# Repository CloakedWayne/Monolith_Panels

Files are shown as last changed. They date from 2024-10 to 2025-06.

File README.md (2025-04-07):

[][cc-by-nc-sa]

# Monolith Panels for Voron 2.4 and Trident

### 1515 extrusion version by CabbageCorp can be found [here](https://github.com/CloakedWayne/Monolith_Panels/tree/main/Usermods/CabbageCorp/Mini_Monolith).

<br/>



Join the Discord (https://discord.gg/JanBKxAzDz)

## What's this?
Overcomplicated panels.



## Use:
- The CAD contains everything that's needed for V2/VT 250/300/350mm with BOM thickness panels (3mm) and is also **a good assembly guide**.

- The vertical printed part length is determined by the theoretical Z travel and NOT the bed size. Pick the vertical part length based on the Z travel of your machine. Tridents usually have a 250mm Z regardless of the bed size, except the cubed kits.

- It's intended to be used with **another layer of 3mm foam tape** or with 5mm foam tape paired with 4mm panels (Monolith Gantry stepper protrusion is 3.6mm).

- Feel free to remix the parts for different setups!

- Parts will load in the correct orientation when exported.

- The corners can be used without the straights, but your mileage may vary if you don't put VHB on them.

- When used as a panel frame you can get away with putting VHB only in the middle.

- Recommended **shrinkage compensation** for the parts when printed in **ABS is 99.3-99.5%**. Make sure to test this before committing to printing huge amounts of plastic, because shrinkage can be 3-4mm in total.

- Clips are fairly sensitive to EM/PA, but can be easily scaled to fit perfectly in the other plastic parts. They're not sensitive to alu extrusion tolerances.



## BOM
### DISCLAIMER: This is a challenging mod and a lot of the stuff is still untested. The BOM quantities can greatly vary based on how you build it. Always refer to CAD.



|No.|Description|Qty|
|---|---|---|
|1.|M3x16 SHCS or BHCS|probably more than 10|
|2.|M3x6 BHCS or M3x8 FHCS (better)|definitely more than 10|
|3.|M3 nuts|probably more than 10|
|4.|M3x5x4mm heatset inserts|definitely more than 10|
|5.|VHB tape|enough|
|6.|Foam tape|enough|
|7.|4mm OD PTFE tube|exactly 96mm|



If you've any got questions you can find me on Discord ***@CloakedWayne***
<br/><br/><br/><br/>
This work is licensed under a
[Creative Commons Attribution-NonCommercial-ShareAlike 4.0 International License][cc-by-nc-sa].

[][cc-by-nc-sa]

[cc-by-nc-sa]: http://creativecommons.org/licenses/by-nc-sa/4.0/
[cc-by-nc-sa-image]: https://licensebuttons.net/l/by-nc-sa/4.0/88x31.png
[cc-by-nc-sa-shield]: https://img.shields.io/badge/License-CC%20BY--NC--SA%204.0-lightgrey.svg

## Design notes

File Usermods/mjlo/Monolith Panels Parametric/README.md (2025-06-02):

# Parametric Monolith Panels

I like Monolith Panels, but I wanted thicker panels to trap more heat. Design is not exactly the same as Wayne's original, more "inspired by".
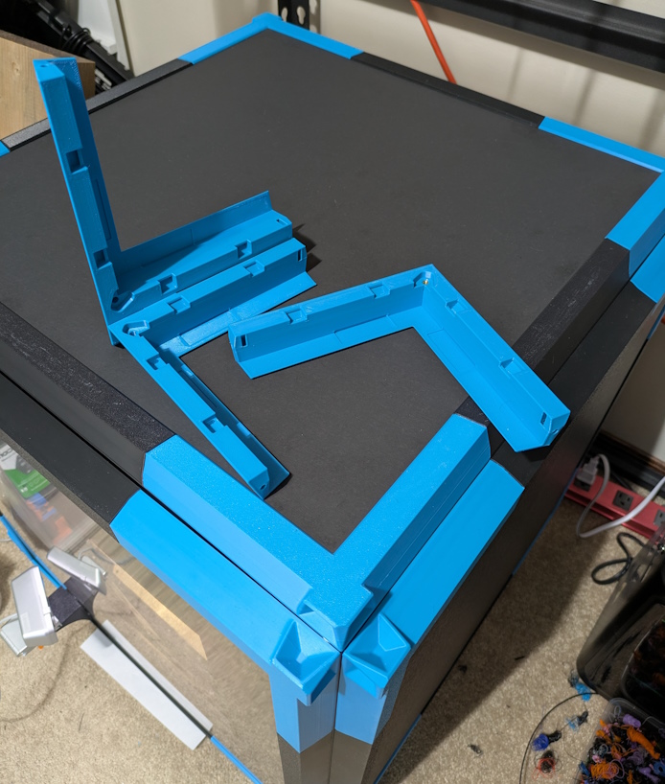
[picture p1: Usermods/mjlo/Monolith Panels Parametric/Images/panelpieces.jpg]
Thicker Monolith Panel pieces


# How to use
Upload the CAD file to fusion, open it, click "Modify" > "Change Parameters". Most parameters have a description or are self explanatory, but I am not good with words so YMMV.

Printing, BOM, and assembly should be pretty much the same as the originals, aside from the change in panel material.

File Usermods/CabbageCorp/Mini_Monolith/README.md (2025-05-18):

# Mini Monolith

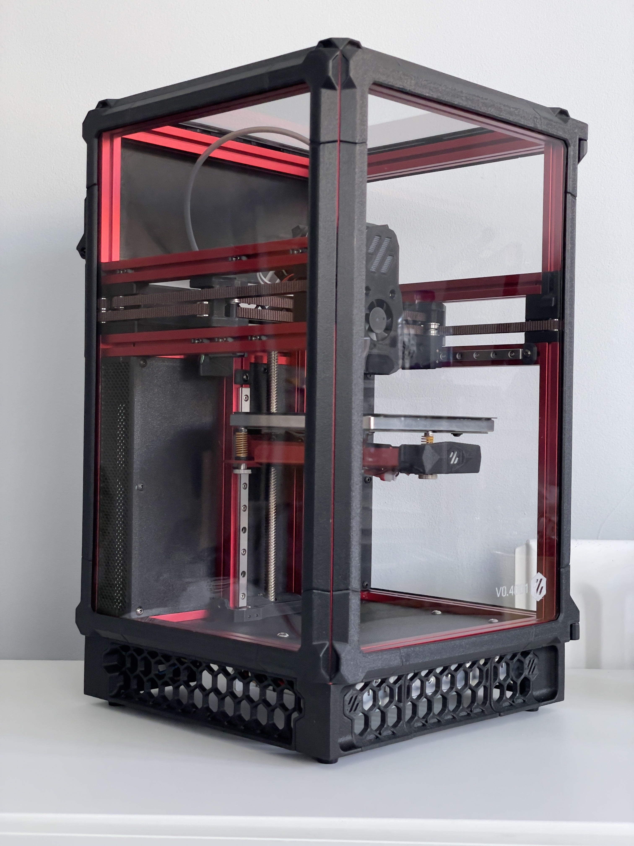
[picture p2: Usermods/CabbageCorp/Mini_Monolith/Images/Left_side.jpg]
Left_side


## Intro

Mini Monolith is an adaptation of monolith panels from CloakedWayne with zeropanel clips from zruncho, adapted for 1515 extrusions and PFA’s.

I’ve seen a couple of really nice mini-monolith versions floating around, and have been waiting for release but needed something for my build so threw this together quickly.

This is currently only sized for 100mm tophat V0.2’s and any PFA variants like the Hex-Zero that has a 348mm vertical height. However, geometry is fairly easy to modify so cutting and extruding would allow different lengths for other PFA’s (please upload and share).

Unfortunately, I forgot that monolith doesn’t have a door closure system for a trident or V0 type hinged door so I’ve just been using 3 clips to keep the door closed. ColonyClacker/Mini Fridge Door can be added with the additional verticals, hardware can be found (soon) on the [ColonyClacker](https://github.com/PrintersForAnts/ColonyClacker) repo. [If you like this project and want to help me get free filament, feel free to drop a like and download cad/stl’s from makerworld here](https://makerworld.com/en/models/1300382-mini-monolith-panels-for-voron-v0-v0-2-1515-pfa#profileId-1332588)

## Why Mini Monolith?

- Full panels sized panels help eliminate leakage through tophat panel gaps
- Compatibility with relaxed fit mini-fridge door panels (329mm x 209mm) for easy sourcing
- Similar panel stack to zero panels (6.8mm total squish height of 1mm VHB + 3mm panel +3mm foam)
- Mini monolith allows 2.8-3mm spacing between the frame and panels -allowing Pandora’s box and Hex-zero variants to have extra space for gantry
- Strong clamping force to enable thicker foam and more squish
- Extrusions covered to minimise heat loss
- Recessed VHB tape slots for 4mm panels + 3mm foam (if you have 3mm panels+3mm foam, attach the VHB to the non-recessed parts of the frame for adequate squish)

### Main changes:

- Heatset inserts instead of trapped nuts to connect sections
- Through bolted heatset screw reinforcement
- Hinges adapted for m3x20 pins commonly found in extruders or PTFE tubes like the original monolith
- Various dimensional changes

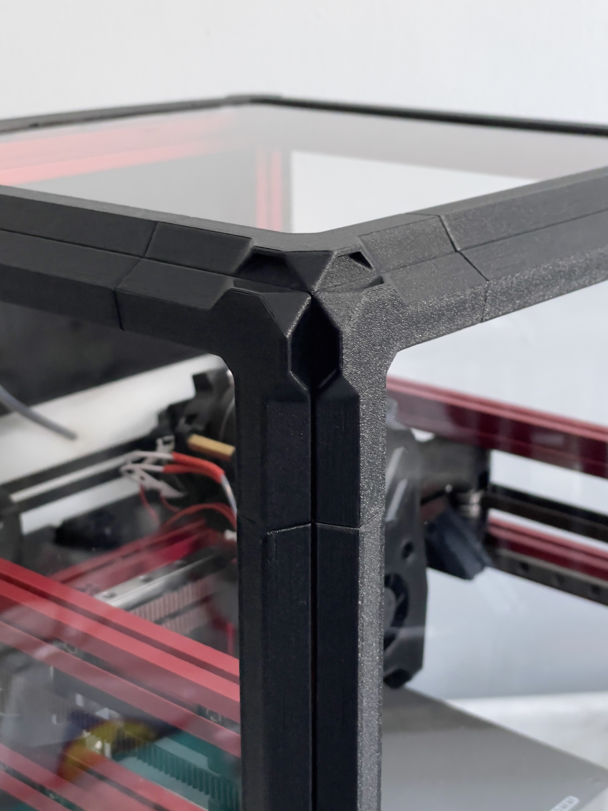
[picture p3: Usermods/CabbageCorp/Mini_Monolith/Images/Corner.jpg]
Corner

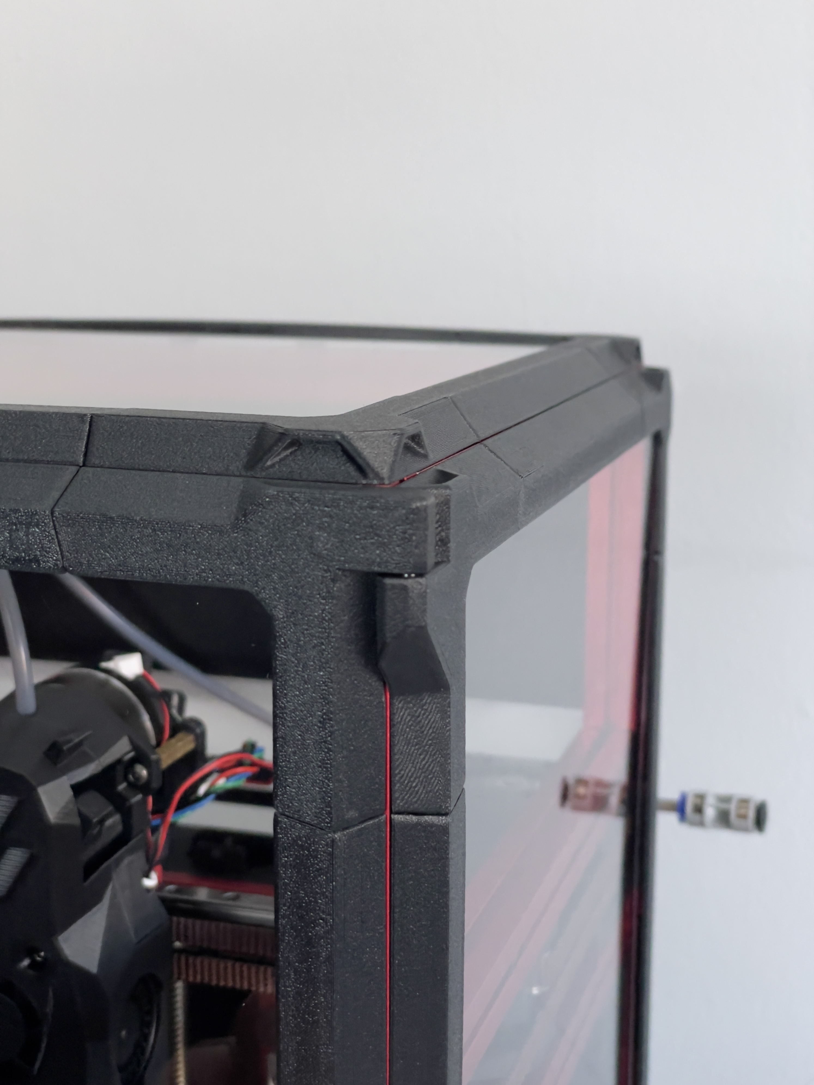
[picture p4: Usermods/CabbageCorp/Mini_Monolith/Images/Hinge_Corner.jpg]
Hinge_Corner

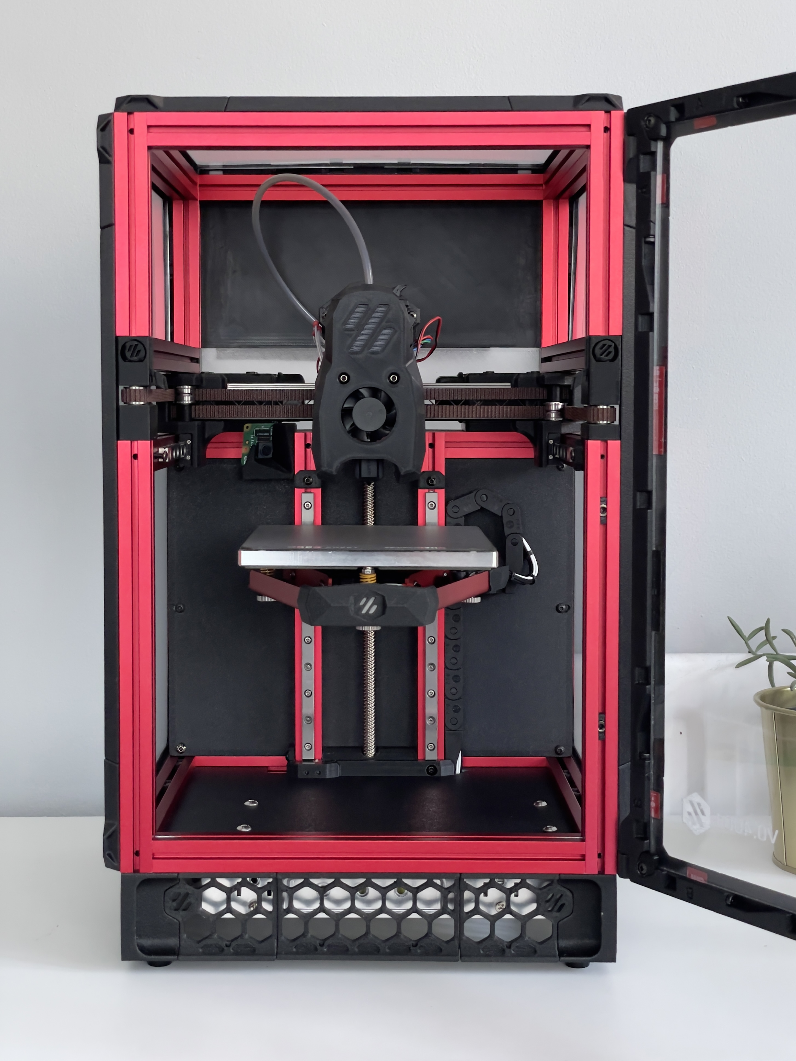
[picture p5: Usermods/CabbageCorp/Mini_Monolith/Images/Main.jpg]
Main

right_side

## BOM

- **Per side/panel**

    | Amount | Part | Notes  |
    | --- | --- | --- |
    | 12 | heatset inserts m3x5x4 (voron) | 3 per corner |
    | 8 | M3 x 16 BHSC/SHSC screws  | (10-16mm works) |
    | 1 roll | 1mm x 5mm VHB foam tape | Voron BOM VHB tape cut in half works |
    | 1 roll | 5-6mm wide, 3-5mm thick foam tape | 4.5m total for 3 panels + Top |
- **Hinges**

    | Part | Notes |
    | --- | --- |
    | 3x20mm pins | Common extruder pins |
    | 18mm PTFE tubes | 4mm OD |
- **Panels**
    
    1-3x Mini Fridge Door panels (relaxed fit 329mm x 209mm)
    
    1x 209x209mm top panel (nominal length of 210.8mm or 212x212mm using the experimental horizontals)
    
    | Qty. | Part | Notes |
    | --- | --- | --- |
    | 3 | Mini Fridge Door panels (3mm thick relaxed fit 329mm x 209mm) | Max dimensions: 329 x 210.8 |
    | 1 | 209x209mm top panel (3mm thick) | Max dimensions: 210.8 x 210.8 |
    | 0 | Experimental 212x212mm top panel (3mm thick) | Due to widening straights, the clips may be pushed towards the centreline and fall out of the printed frame easier |
- **Full coverage (2 Sides, Door and Top)**

    | Amount | Part | Notes  |
    | --- | --- | --- |
    | 48 | heatset inserts m3x5x4 (voron) | 3 per corner |
    | 32 | M3 x 16 BHSC/SHSC screws  | (10-16mm works) |
    | 1 roll | 1mm x 5mm VHB foam tape | Voron BOM VHB tape cut in half works |
    | 4.5M | 5-6mm wide, 3-5mm thick foam tape | 4.5m total for 3 panels + Top |
    | 2x | 3x20mm pins or 18mm PTFE tubes | 2 pins or 32mm ptfe total |
    | 3 | Mini Fridge Door panels (3mm thick relaxed fit 329mm x 209mm) | Max dimensions: 329 x 210.8 |
    | 1 | 209x209mm top panel (3mm thick) | Max dimensions: 210.8 x 210.8 |

## **Print notes:**

Like monolith, this is scaling/shrinkage sensitive with no compensation built in so tuned print profiles are strongly recommended. 

- Thin areas around screw access cutouts and corners are PA sensitive.
- Optional mouse ears on the longer sections are recommended for those that typically struggle with adhesion.
- If second layer perimeters are separating, turning off elephants foot compensation and dialing in first layers may help.
- The clips are the most sensitive part so make sure EM is perfect -if they are too loose, scaling them up slightly by 0.5-1% will help with hold.
- The model works best with 0.1mm increments but will still work fine at 0.2mm layer heights with no differences in testing. Initial layer height of 0.1 should work as well but is currently untested.
- Each panel will need 4 corners, either universal or hinged with 2 horizontals and 2 vertical straights. For 3 sided monolith and a tophat, you’d need to print:
    - 12x universal corners
    - 4x hinges
    - 6x vertical sections
    - 10x horizontal sections

*note: There is an experimental topside horizontal for stock 212x212mm panel size however, the extra width tilts the clips towards the centre. Frequent removal will likely result in loosening and clips being pulled out of the panels due to angle. Larger clip recommended.*

## **Assembly notes:**

Use the heatset tool to prevent bulging on the thin walls 




Ensure heatsets are fully inserted flush with the lowest edge

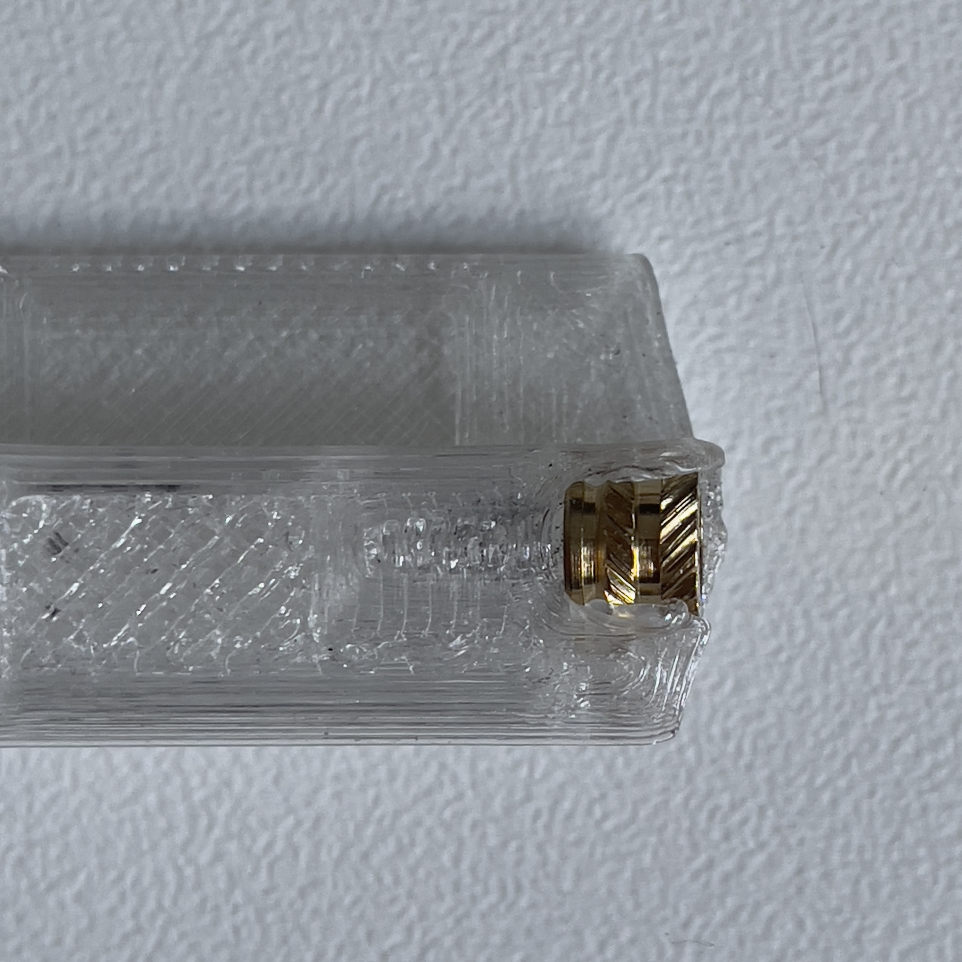
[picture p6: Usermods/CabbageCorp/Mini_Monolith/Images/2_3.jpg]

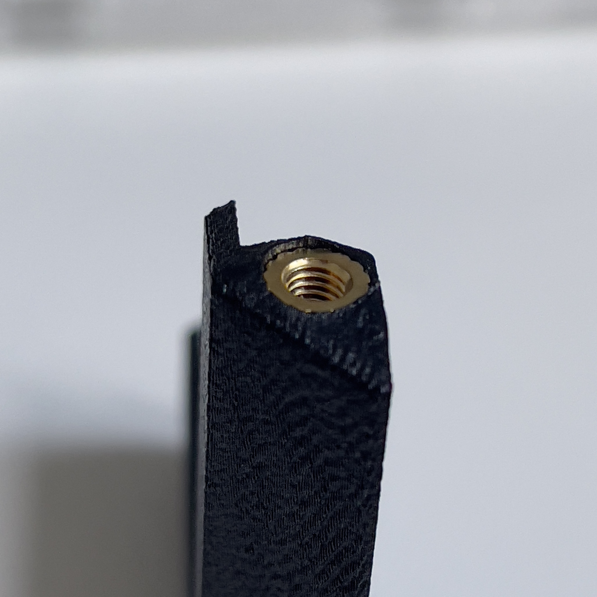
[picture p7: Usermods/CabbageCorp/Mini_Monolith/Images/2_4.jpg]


Press clips in firmly with something firm

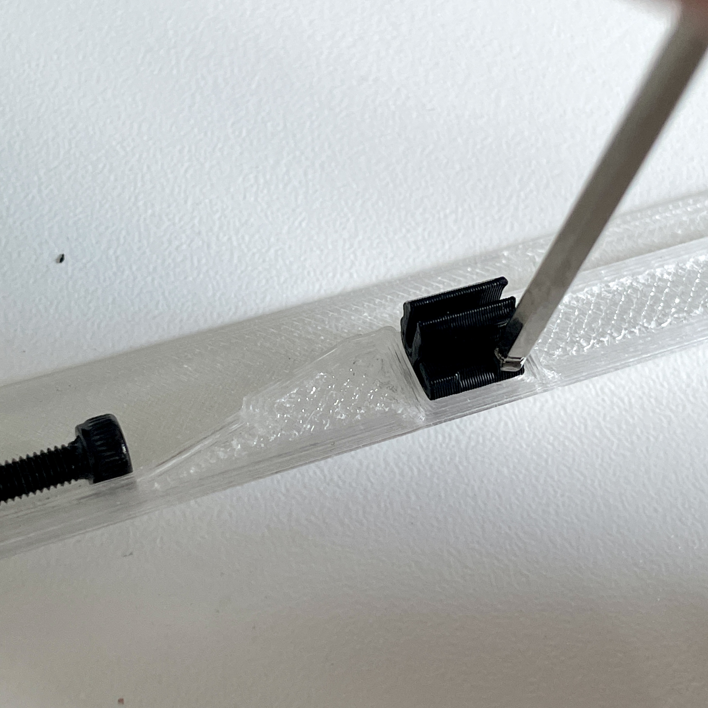
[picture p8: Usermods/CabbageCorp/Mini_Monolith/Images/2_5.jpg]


Corner panel clips: ensure the screws are fully tight and lower than flush with the frame.

Optional:

If using screws longer than 10mm, prethread the plastic by screwing it into corner before attaching the straight. To prevent heatset pull out, maintain pressure while tapping the plastic past the insert. 16mm M3 screws will add a bit of rigidity and help with heatset pull out.

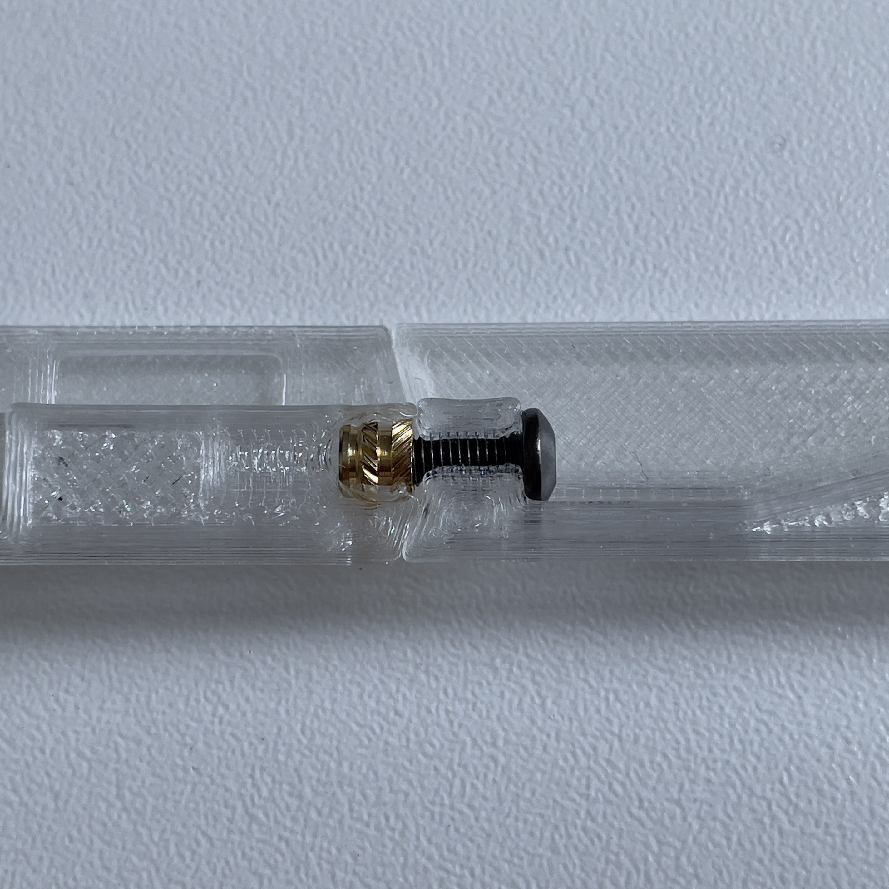
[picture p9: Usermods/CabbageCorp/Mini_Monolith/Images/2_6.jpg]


10mm minimum length

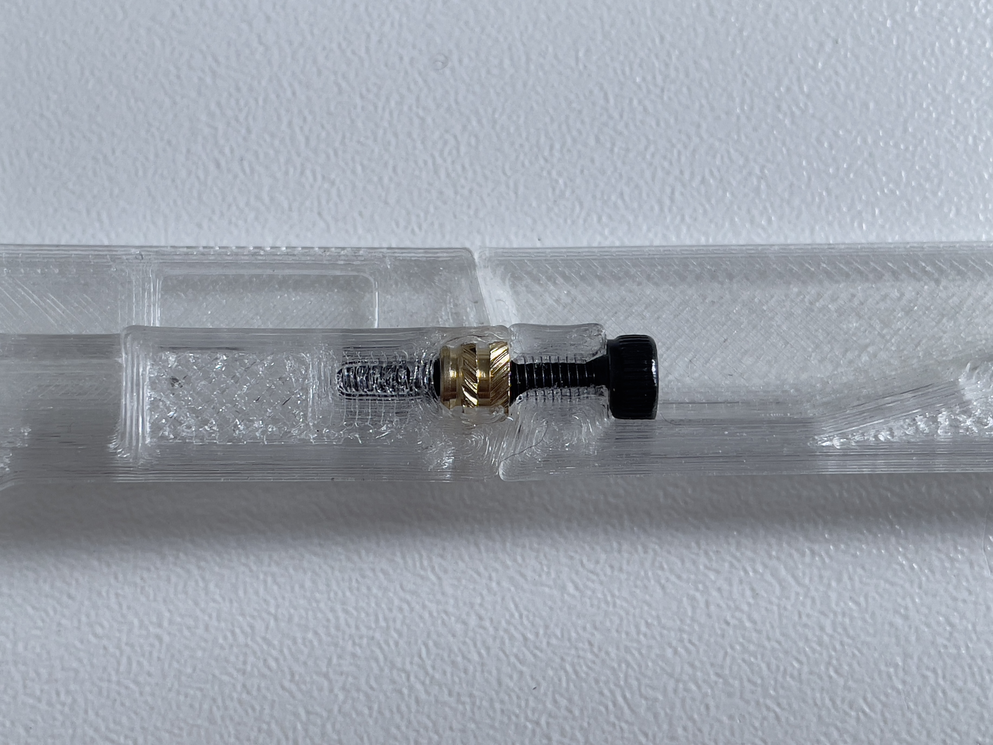
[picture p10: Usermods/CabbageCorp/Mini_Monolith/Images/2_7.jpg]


16mm Maximum length 

I’d like to give a big thanks to these people for their contribution that made this possible:

- CloakedWayne for his monolith design, concept, and amazingly neat/organised and easy to edit cad
- zruncho for his zeropanel clip geometry and research on panel stack
- #sonny5578, #chefha, and #brexited on Voron discord for teaching me cad and inputs
- Ukutghost #hamido. #simonsaysty - special thanks to you guys for wasting filament, beta testing tolerances, finding print issues and giving suggestions.
- #tigsteruk and Ukutghost- for being enthusiastic and helping me feel like my cad isn’t too janky to be shared
- #seti118- for getting panels to me so fast

License note:

Zruncho's ZeroPanels clip geometry retains its original licence that can be found [here](https://github.com/zruncho3d/ZeroPanels?tab=GPL-3.0-1-ov-file#readme).

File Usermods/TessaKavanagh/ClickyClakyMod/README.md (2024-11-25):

# TessaKavanagh ClickyClakyMod
##Acknowledgments:
Special thanks for additions, goes to: 
@luxflow (optional 5mm parts and documentation)

## Spacer

- If you want to use the original clickyclaky parts, print spacers from [STLs/Monolith_Panels_ClickyClackyMod v2.3mf](STLs/Monolith_Panels_ClickyClackyMod%20v2.3mf)
  - There are two types of spacers (see below) 
  - The left one is for handle hinges (print twice), and the right one is for handle latch (print once).
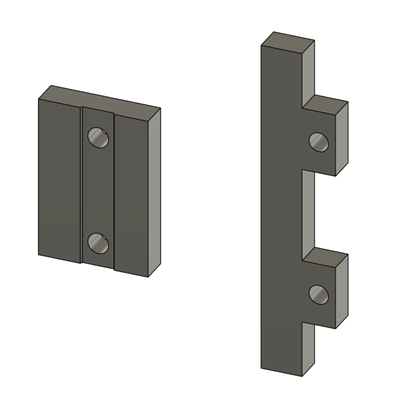
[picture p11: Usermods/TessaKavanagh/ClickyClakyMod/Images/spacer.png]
spacer

- If you don't want to use spacers, reprint the modded clickyclaky parts in [STLs/optional](STLs/optional/)

## Assembly

- To insert the door hinge side (mostly left side) monolith panels, you must detach door first.

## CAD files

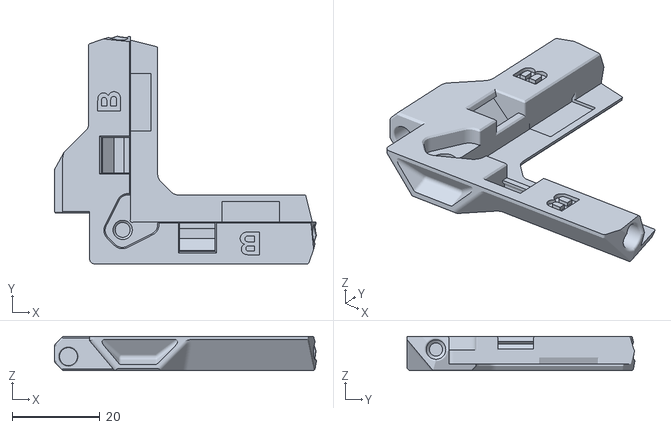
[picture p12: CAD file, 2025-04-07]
Usermods/CabbageCorp/Mini_Monolith/STLs/18mm PTFE Hinge/18mm Ptfe [a]_hinge_b.stl
59.8 x 52.0 x 7.80

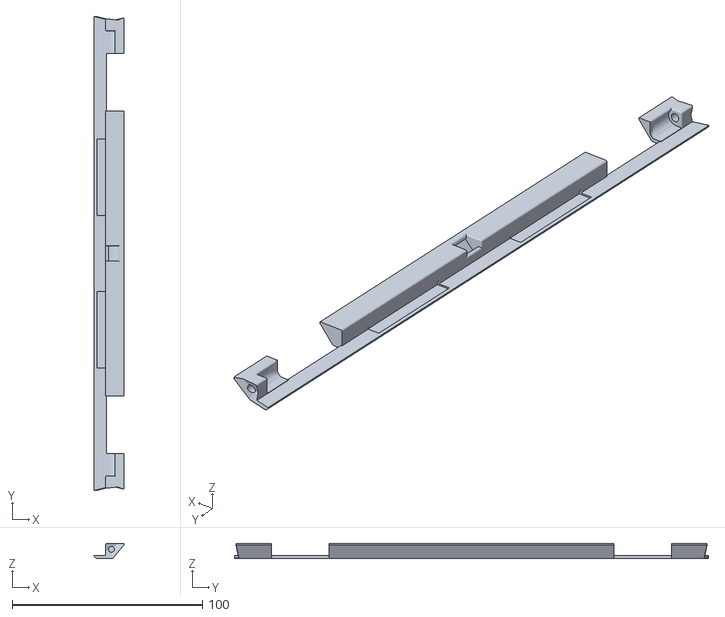
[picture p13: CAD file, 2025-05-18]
Usermods/CabbageCorp/Mini_Monolith/STLs/ColonyClacker Verticals/CC Hinge Vertical.stl
15.8 x 249.2 x 7.80

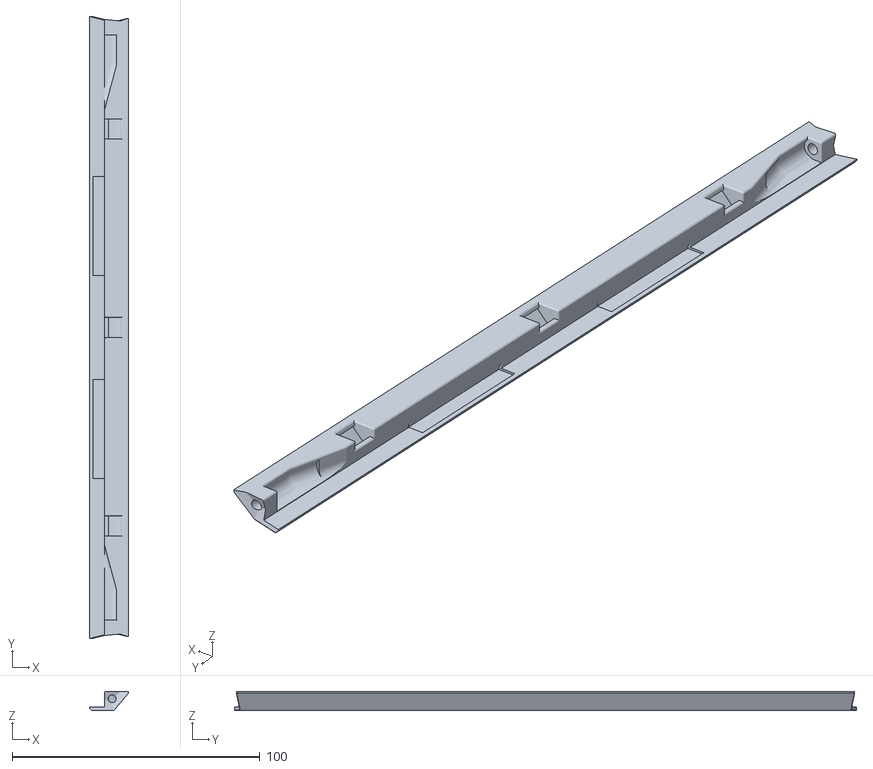
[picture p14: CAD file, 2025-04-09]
Usermods/CabbageCorp/Mini_Monolith/STLs/Pandora 350mm Vertical.stl
15.8 x 251.0 x 7.80

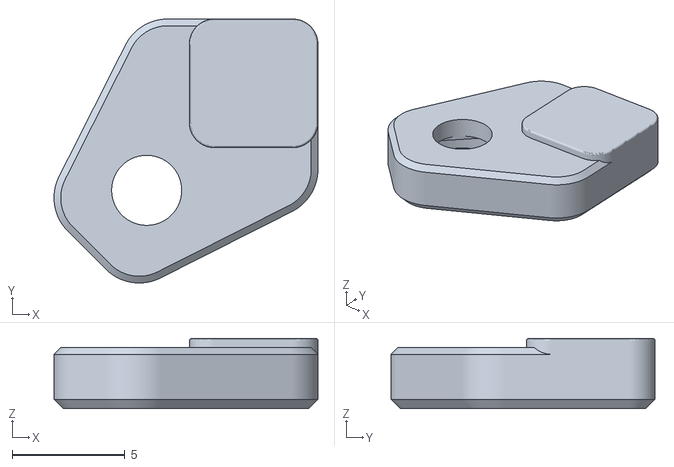
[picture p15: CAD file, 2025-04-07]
Usermods/CabbageCorp/Mini_Monolith/STLs/Panel Corner Clamp/3mm corner_clamp_BHCS_x16.stl
11.7 x 11.7 x 3.10

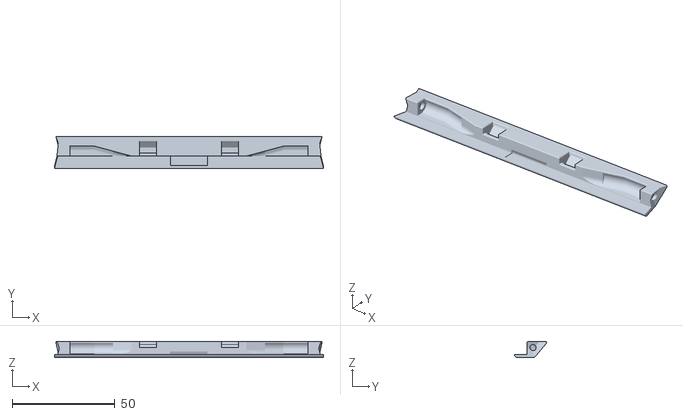
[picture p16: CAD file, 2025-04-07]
Usermods/CabbageCorp/Mini_Monolith/STLs/Straight Sections/Horizontal 210.8mm.stl
131.0 x 15.8 x 7.80

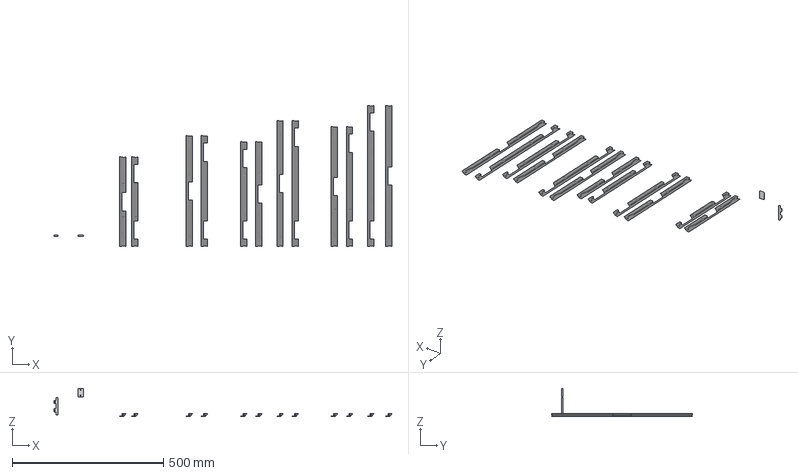
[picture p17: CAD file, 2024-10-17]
Usermods/TessaKavanagh/ClickyClakyMod/STLs/Monolith_Panels_ClickyClackyMod v2.3mf
1118.1 x 468.0 x 94.0 mm
Körper1 x 2
Körper3 x 11
Körper4
Körper5
Körper6
Körper7

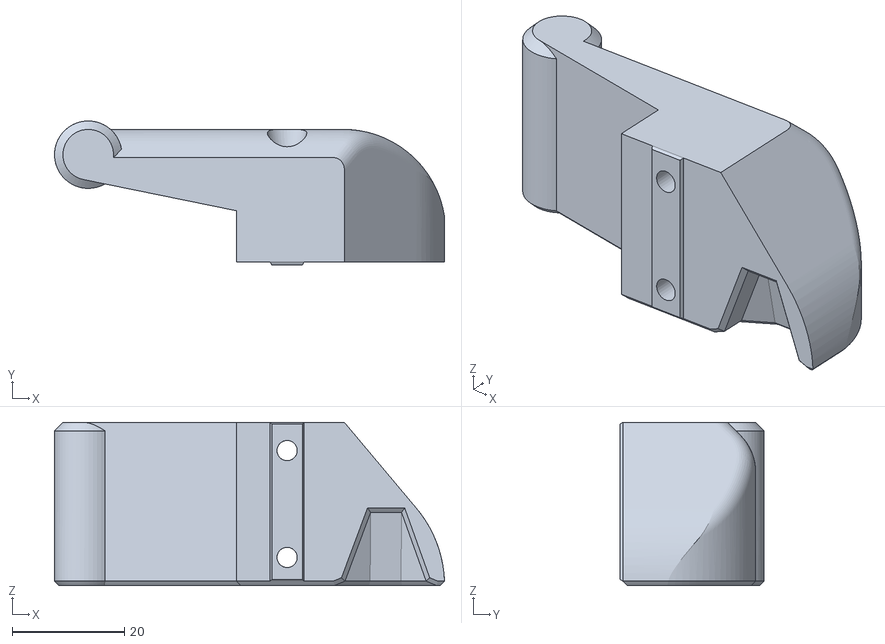
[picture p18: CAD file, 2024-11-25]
Usermods/TessaKavanagh/ClickyClakyMod/STLs/optional/Hinge_Top.stl
69.3 x 25.6 x 29.0

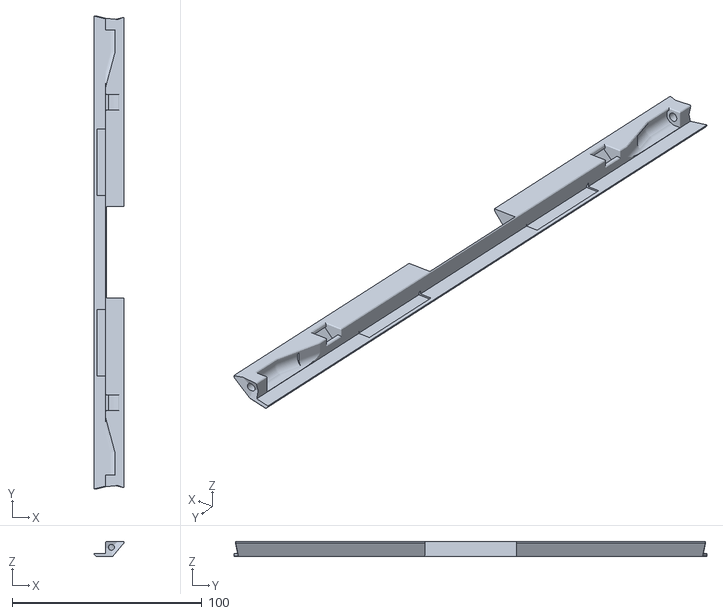
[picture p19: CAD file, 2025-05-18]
Usermods/CabbageCorp/Mini_Monolith/STLs/ColonyClacker Verticals/CC Handle Vertical.stl
15.8 x 249.2 x 7.80

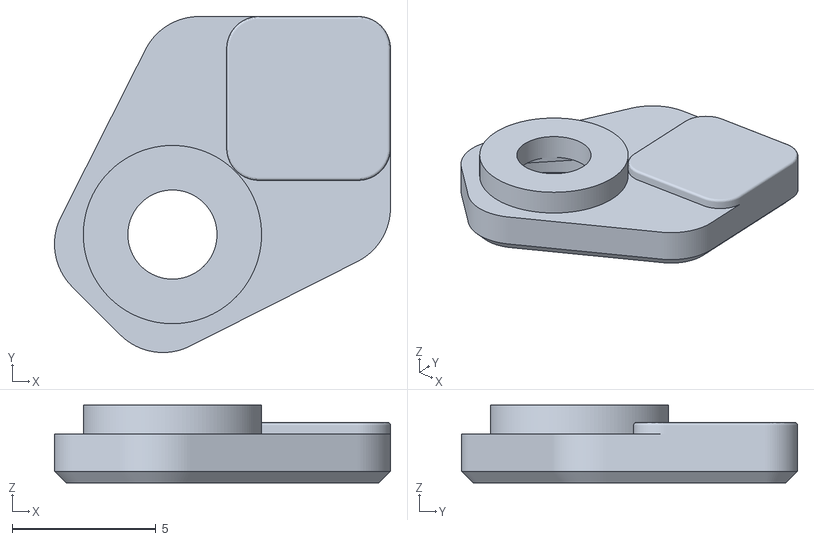
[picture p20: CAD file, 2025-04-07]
Usermods/CabbageCorp/Mini_Monolith/STLs/Panel Corner Clamp/4mm corner_clamp_BHCS_x16.stl
11.7 x 11.7 x 2.70

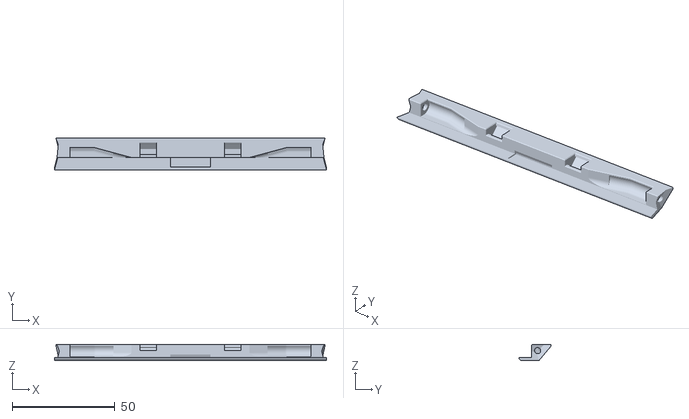
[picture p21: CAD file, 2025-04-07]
Usermods/CabbageCorp/Mini_Monolith/STLs/Straight Sections/Horizontal (Experimental 212.8mm).stl
132.2 x 15.8 x 7.80

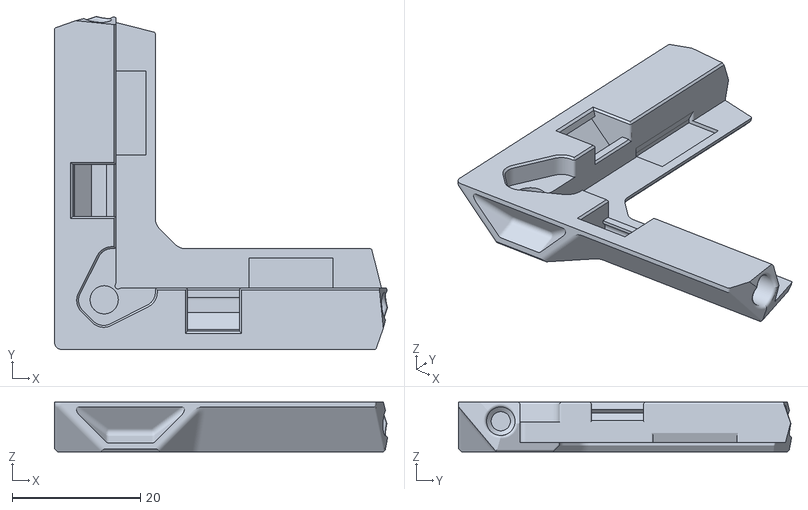
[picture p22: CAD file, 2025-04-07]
Usermods/CabbageCorp/Mini_Monolith/STLs/Universal Corner.stl
52.0 x 52.0 x 7.80

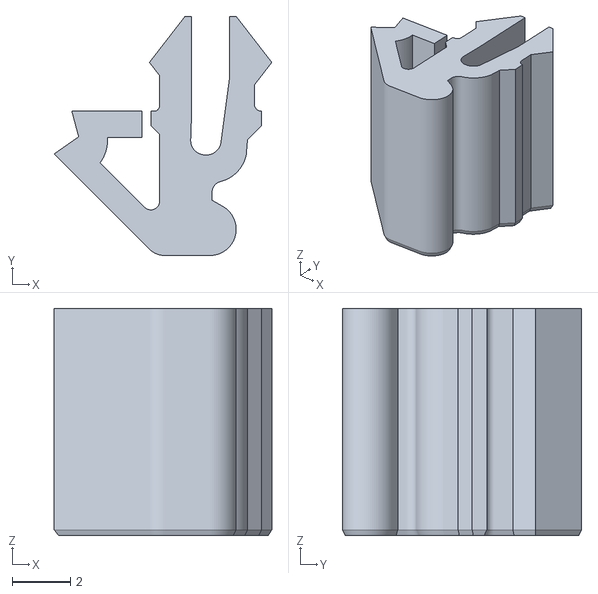
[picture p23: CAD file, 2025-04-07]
Usermods/CabbageCorp/Mini_Monolith/STLs/Clip (7.8mm).stl
7.47 x 8.20 x 7.80

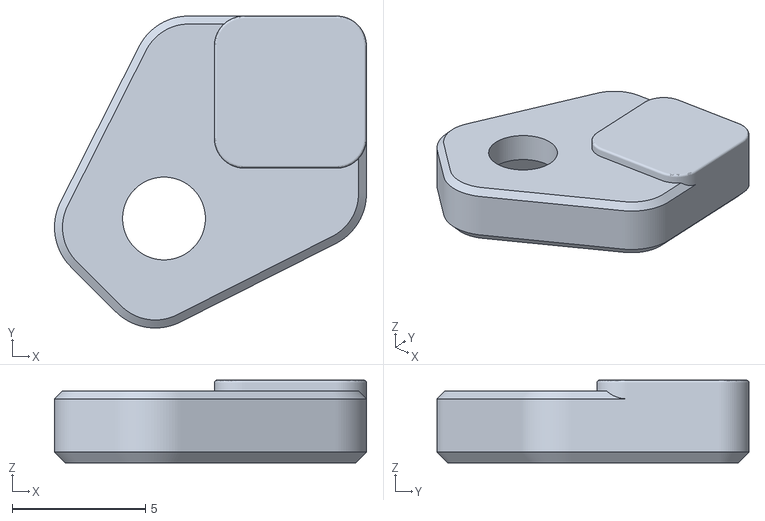
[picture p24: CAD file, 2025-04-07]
Usermods/CabbageCorp/Mini_Monolith/STLs/Panel Corner Clamp/3mm corner_clamp_FHCS_x16.stl
11.7 x 11.7 x 3.10

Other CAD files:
Usermods/CabbageCorp/Mini_Monolith/STLs/18mm PTFE Hinge/18mm Ptfe [a]_hinge_c.stl
Usermods/TessaKavanagh/ClickyClakyMod/STLs/optional/Hinge_Bottom.stl
Usermods/CabbageCorp/Mini_Monolith/STLs/18mm PTFE Hinge/18mm Ptfe [a]_hinge_a.stl
Usermods/CabbageCorp/Mini_Monolith/STLs/Straight Sections/Vertical 348mm.stl
Usermods/CabbageCorp/Mini_Monolith/STLs/18mm PTFE Hinge/18mm Ptfe [a]_hinge_d.stl
Usermods/CabbageCorp/Mini_Monolith/STLs/Heatset Insert Tool.stl
Usermods/CabbageCorp/Mini_Monolith/STLs/M3x20 Pin Hinge/M3x20 Pin [a]_hinge_A.stl
Usermods/CabbageCorp/Mini_Monolith/STLs/M3x20 Pin Hinge/M3x20 Pin [a]_hinge_B.stl
Usermods/CabbageCorp/Mini_Monolith/STLs/M3x20 Pin Hinge/M3x20 Pin [a]_hinge_C.stl
Usermods/CabbageCorp/Mini_Monolith/STLs/M3x20 Pin Hinge/M3x20 Pin [a]_hinge_D.stl
Usermods/TessaKavanagh/ClickyClakyMod/STLs/optional/Handle.stl
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

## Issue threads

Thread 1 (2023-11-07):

How we can buy you a Coffee?

Shamoon78, 2023-11-07:

CloakedWayne, 2023-11-09:
I'm glad you like my work! I added a link to my Ko-fi page.

Shamoon78, 2023-11-10:
And how to find your KO-fi page?

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

CloakedWayne, 2023-11-10:
The white icon is a link. I guess I'll have to make that more clear.

Shamoon78, 2023-11-10:
Honestly, I have no Idea which white icon you are talking about. I am a bit
old school and not quick with web things .

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

CloakedWayne, 2023-11-10:
Sorry, I'll make improvements.

[](https://ko-fi.com/cloakedwayne)

Shamoon78, 2023-11-10:
I found it but this Ko-fi is only Paypal , I have no paypal and I donot
like it. What a shame.🥴

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

Closed 2023-11-09.

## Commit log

2023-10-06 CAD added
2024-05-05 Add files via upload
    Modified Top Corner for Clicky Hinge Clearence
    [ClickyCornerModified.3mf]
2024-10-17 Add files via upload
    Bugfix for Tritent 250 Parts
    [Monolith_Panels_ClickyClackyMod v2.3mf]
2024-10-17 removed V1 files
    [ClickyCornerModified.3mf]
2024-11-23 Added docs, optional 5mm padded clickyclacky parts
    [Handle.stl, Hinge_Bottom.stl, Hinge_Top.stl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]
2025-04-07 added Mini Monolith
    [Handle.stl, Hinge_Bottom.stl, Hinge_Top.stl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]
2025-04-07 added STLs
    [18mm Ptfe [a]_hinge_a.stl, 18mm Ptfe [a]_hinge_b.stl, 18mm Ptfe [a]_hinge_c.stl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]
2025-04-08 Create Pandora's box 350mm height Vertical
2025-05-17 Delete Usermods/CabbageCorp/Mini_Monolith/CAD/Mini Monolith.f3d
    updated new cad to include PB 350mm height verticals and ColonyClacker Hinges
2025-06-01 Added Monolith Panels Parametric usermod
    [Monolith Panels Parametric.f3d]

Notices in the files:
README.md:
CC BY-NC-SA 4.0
